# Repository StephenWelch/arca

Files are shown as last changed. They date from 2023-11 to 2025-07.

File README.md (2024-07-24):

## Members
Stephen Welch, Computer Engineering Student (2024)
stephenwelch@vt.edu

## Mentor
MENTOR NAME HERE

## Current Status
IN PROGRESS

### 7-24-24
- Prototype of full assembly design
- Work-in-progress hardware-sim abstraction layer
- Assembly & validation of updated left leg in progress
- Full model exported to URDF & MJCF
- Solved design issues:
  - Knee actuator didn't have enough clearance with sideplate to freely rotate
  - Knee joint was prone to friction with thigh sideplates
  - Thigh joint was prone to friction with lower thigh carriage
  - Hip motor mounting didn't have enough clearance to assemble without flex
  - Foot had no way to add rubber/other material for more friction
  - Width of knee joint made fastening bearings hard
- Current design issues:
  - Most fasteners are M3/M4 nuts & bolts - unknown how this will stand up to vibration
  - Rod end bearing range-of-motion is biggest limiter of robot range-of-motion
  - Backlash
    - Fasteners for 3D printed linkage arms to motor shaft have a lot of play
      - Linkage arm thru-hole tends to compress
        - Currently testing clamp-style design
      - M3 through motor shaft thru-hole is not perfect fit
        - May need to switch to steel pin
      - No off-the-shelf servo arms for motor shaft size
    - Several parts are very thin & flexible in the non-vertical direction in order to reduce size and make assembly easier
    - Mounting for thigh arms is not ideal & may flex
      - Planning on addressing this by integrating into thigh sideplates once finalized
  - Clearance and wire routing
    - Planning on investigating materials to reduce friction between motor wires & PLA parts

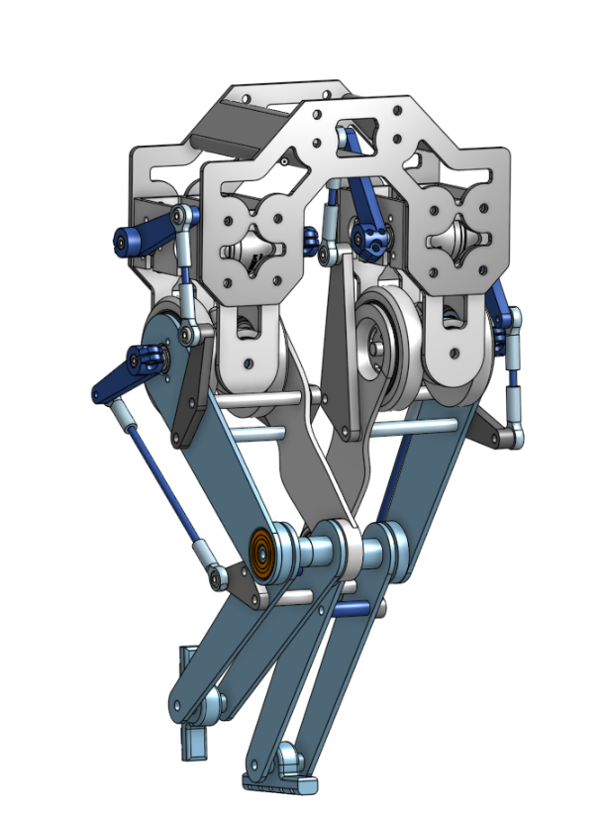
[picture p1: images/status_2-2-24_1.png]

  
### 2-2-24
- Test fit of (most of) 1st iteration design
- Waiting for electronics & test stand parts
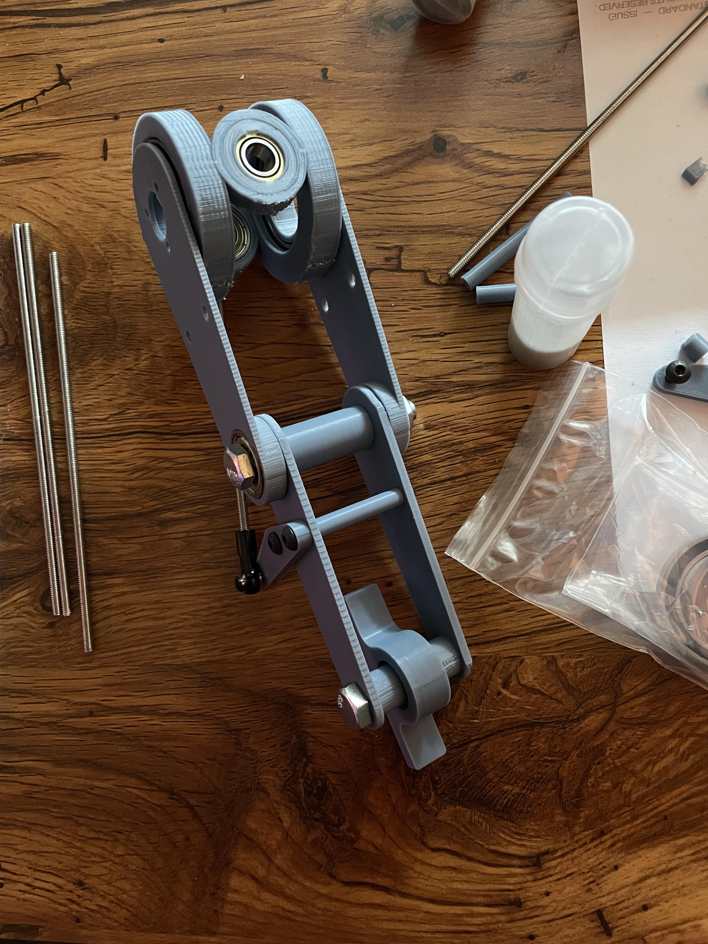
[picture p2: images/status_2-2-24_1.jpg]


## Project Overview

A torque-controlled bipedal robot for <$1000. The short term goal is assembling and validating a single leg under load.

## Educational Value Added

- Learning how to CAD complex moving assemblies
- Embedded controls
    - Implement torque control for robot joints
    - Serial interface to high-level controller
- High-level controls
    - ROS 2
    - Implementing [step timing adaptation-based walking controller](https://ieeexplore.ieee.org/stamp/stamp.jsp?arnumber=9082021)
    - Implementing [MPC walking control](https://arxiv.org/pdf/2010.08198.pdf)
    - Impedance control
    - Whole body control

## Tasks

<!-- Your Text Here. You may work with your mentor on this later when they are assigned -->

## Design Decisions

### Electronics
- Tethered operation to reduce cost
    - Battery, RPi, Power electronics to be added later
- Teensy commanded over serial by PC running high-level controller
- Robomaster M2006 P36 Brushless Motor
    - 1 Nm torque @ 1:36 reduction
    - 90g motor, 17g ESC
    - Pros:
      - Only brushless motor of its size supporting torque control out-of-the-box
      - [Proven performance](https://www.youtube.com/watch?v=_Sh4kRtmAog)
      - Constant torque at all RPMs
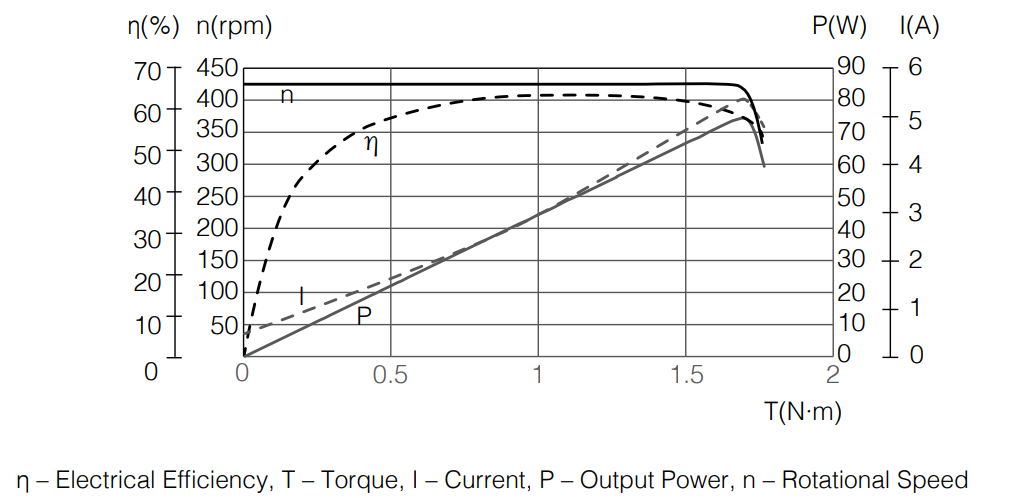
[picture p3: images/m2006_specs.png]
M2006 motor curves
        
    - Cons:
      - High reduction -> low torque transparency -> less compliance
      - Form factor challenging to package

### Mechanics
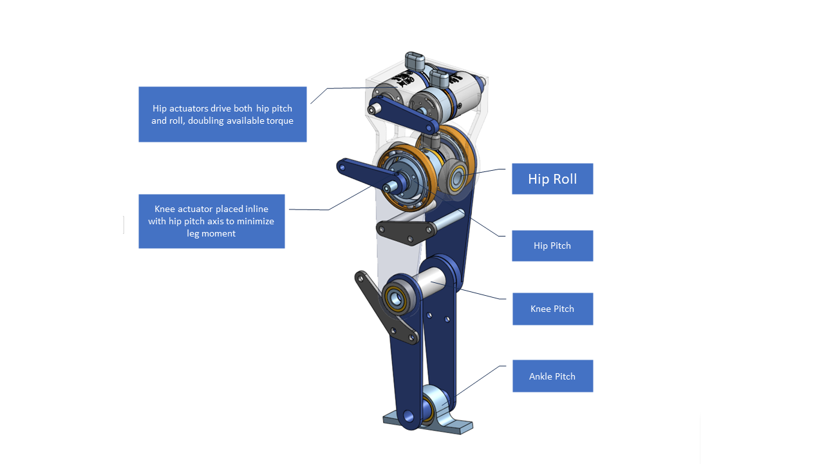
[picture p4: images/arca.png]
labeled diagram of leg

- 3 DoF per-leg
    - Pros:
        - Each actuator removed from the design saves $94
        - Reduces mechanical complexity
    - Cons:
        - Since the ankle isn't actuated, the robot is *not* passively stable - it must actively step to maintain balance
            - This makes control more challenging
        - Since hip yaw isn't actuated, the robot yaw can't be controlled directly while walking
- Actuator arrangement
    - Based on Tello Leg: [Video 1](https://www.youtube.com/watch?v=62lo04Up2vc) [Video 2](https://www.youtube.com/watch?v=mn8tCtYHzHI&t=1s) [Paper](https://arxiv.org/abs/2203.00644)
        - Challenging practical limitation to this design is rotor inertia of QDD actuators, especially at the knee/ankle differential. The P36 is not QDD and is much smaller scale, removing this limitation
    - Minimizes "reflected inertia" - the moment of inertia of each link the actuator has to move
    - Keeps knee actuator in the leg frame, which reduces torque tracking requirements
    - Combined hip/roll axes
        - Rarely actuated at the same time, effectively doubles available torque to 2 Nm
- Avoid gear/belt transmissions where possible
    - Large losses to friction, etc. esp. at this scale
    - Hard to get right, esp. with 3D prints
- Available torque
    - 1 N*m * 0.2248089431 lbf/N \* 100 cm/m = 22.48 lbf\*cm
    - Actuator linkages designed to be 1:1
    - Assuming 90 deg knee bend:
        - Knee can lift 22.48 lbf\*cm / 8 cm thigh length = 2.81 lbf
        - Thigh can lift 22.48 lbf\*cm * 2 motors / 8 cm thigh length = 5.62 lbf
        - Total weight of components is 107 g per actuator * 0.00220462 lbs/g * 3 actuators = 0.707685 lbs

## Design Misc

The main concern is that torque output won't be adequate for dynamic motions (the static case is addressed briefly above).
Possible fixes for this would include:
- Redesigning for larger, higher-torque actuators
- Designing a custom reduction for the M2006 motor
- Adding an effective reduction in the actuator linkages

## Steps for Documenting Your Design Process

<!-- Your Text Here. You may work with your mentor on this later when they are assigned -->

## BOM + Component Cost
[BOM Link](https://docs.google.com/spreadsheets/d/1Qe1dRF8I_yPayQ6RHrJmCSCA597qFWhmrA_jtBt1tgA/edit?usp=sharing)

## Timeline

[Timeline Link](timeline.pdf)

## Useful Links

[CAD](https://cad.onshape.com/documents/4743a97557c0a80d1585b0a7/w/2d6986bf76e2e55acb049bf2/e/10cf3b3fefc155c08becdc5d)
[C610 Motor Controller Library](https://github.com/stanfordroboticsclub/DJIC610Controller)
[BOLT Biped Driver](https://github.com/open-dynamic-robot-initiative/bolt)
[BRUCE Paper](https://ieeexplore.ieee.org/stamp/stamp.jsp?tp=&arnumber=9811790)

## Log

<!-- Your Text Here. You may work with your mentor on this later when they are assigned -->

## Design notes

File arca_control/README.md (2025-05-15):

# Arca Sim

Control code and simulator for the Arca biped.

## Getting started
- [Import a Model](#importing-a-model)
- [Start the simulator](#starting-the-simulation)

## Starting the simulation
Run `uv run scripts/sim.py --model <model_type>`, where `model_type` is a directory under `models`

## Importing a Model
Model paths follow this format: `models/<model_type>/<urdf|mjcf>`. 
- Each subfolder should have its own `config.json` for `onshape-to-robot`. 

Download the model into its corresponding path by running `uv run scripts/import_model.py --model <model_type>`. 

The available model types are:
- `full`: Models all linkages in the robot model
- `reduced`: Models only the pin joints of the robot

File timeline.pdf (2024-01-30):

PHASE ONE: Projected completion by Mar 2, 2024

The deliverable/objective of phase one is to complete a demonstration showing compliance between a motor controller and brushless dc motor. The objective is to write/implement the code required to allow for torque control on a teensy microcontroller. Must include bidirectional communication between microcontroller and motor controller such that the microcontroller uses the torque output to calculate a change in force applied by the motor.

Measure the torque applied by the motor on an actuator linkage. Demonstrate that a force of a specific magnitude can be generated.

This phase may be designed with the use of a harness as a power source instead of a battery.

This phase may include some 3D printing in order to build a linkage/joint. This phase require the design of the 3D printed linkages required to build the robot leg.

COST:

Part Name | Quantity | Unit Price
RM-C610 Brushless Motor Controller (https://store.dji.com/product/rm-c610-brushless-dc-motor-speed-control) | 1 $39.00
RM-M2006-C610 Brushless Motor (https://store.dji.com/product/rm-m2006-p36-brushless-motor) | 1 $55.00
Teensy 4.1 (https://www.amazon.com/PJRC-Teensy-4-1-Without-Pins/dp/B088D3FWR7)) | 1 | $34.60
6656K118 Ultra Thin Ball Bearing (https://www.mcmaster.com/products/bearings/ball-bearings~/ultra-thin-ball-bearings-6/) | 2 $15.65
Skate Bearings (https://www.amazon.com/gp/product/B08YN6WQXR/ref=sw_img_1?smid=AED51UXSJ2INU&psc=1) | 1 | $8.99
TOTAL | | $169.89 + tax/shipping

PHASE TWO: Projected Completion May 1, 2024

The deliverable is a complete robot leg. This leg will be composed of 3 motor/controller pairs each with torque control.

Demonstrate implementation of a walking algorithm successfully actuating the leg.

This phase will include the 3D printing of the parts required to build BOTH robot legs and the parts required to join the robot legs. This phase may include the design of the power electronics to operate the legs independently of a benchtop supply or may continue to use a benchtop supply.

COST: (ADDITIONAL PARTS TO PURCHASE)

Part Name | Quantity | Unit Price
RM-C610 Brushless Motor Controller (https://store.dji.com/product/rm-c610-brushless-dc-motor-speed-control) | 2 $39.00
RM-M2006-C610 Brushless Motor (https://store.dji.com/product/rm-m2006-p36-brushless-motor) | 2 $55.00
6656K118 Ultra Thin Ball Bearing (https://www.mcmaster.com/products/bearings/ball-bearings~/ultra-thin-ball-bearings-6/) | 2 $15.65
Skate Bearings (https://www.amazon.com/gp/product/B08YN6WQXR/ref=sw_img_1?smid=AED51UXSJ2INU&psc=1) | 1 | $8.99
TOTAL | | $228.29 + tax/shipping

PHASE THREE: Projected Completion TBD

Build a second leg. Use both legs together in order to demonstrate a functioning bipedal robot.

COST: TBD

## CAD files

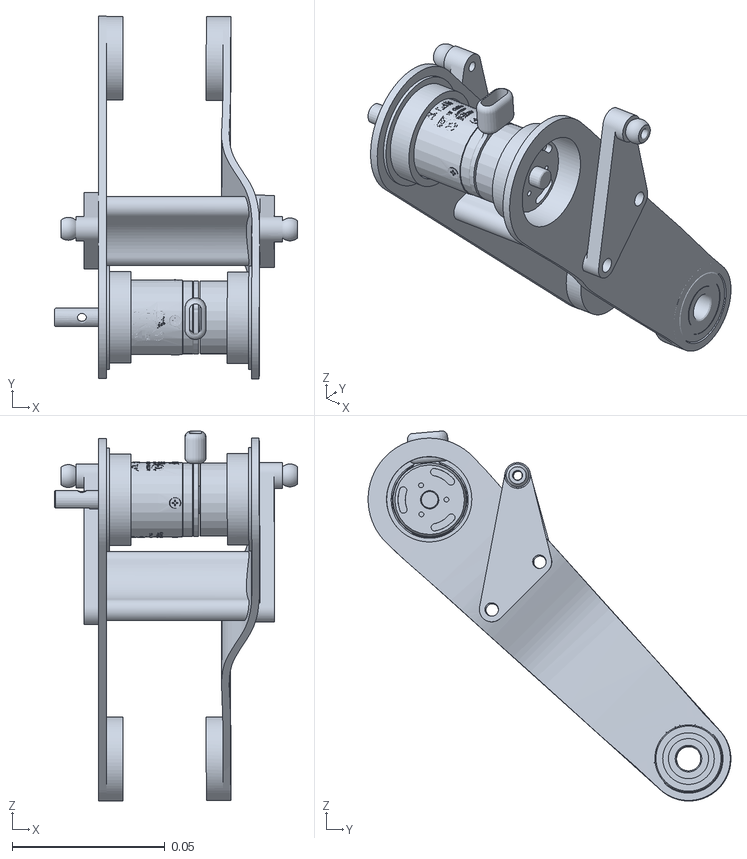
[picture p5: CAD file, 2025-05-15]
arca-sim/models/full/mjcf/assets/merged/r_thigh_visual.stl
0.0796 x 0.119 x 0.121

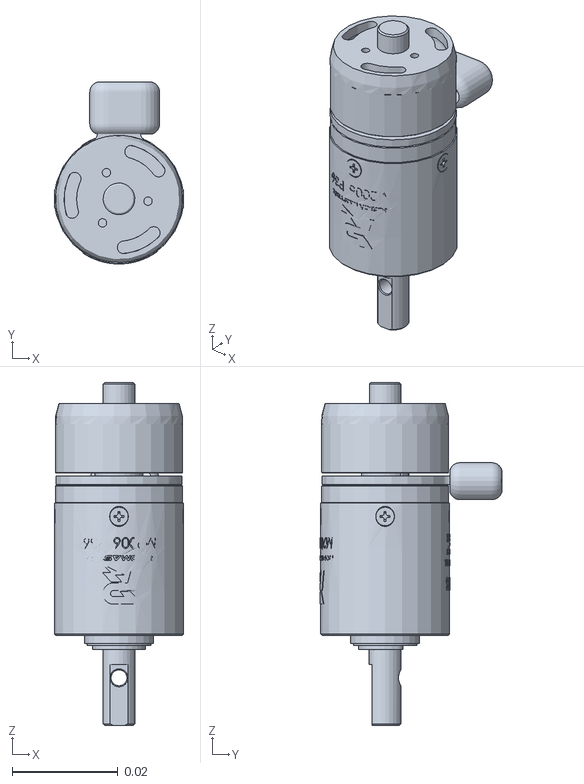
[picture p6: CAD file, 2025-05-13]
arca_control/models/full/mjcf/assets/m2006_p36_3.stl
0.0244 x 0.0344 x 0.0648

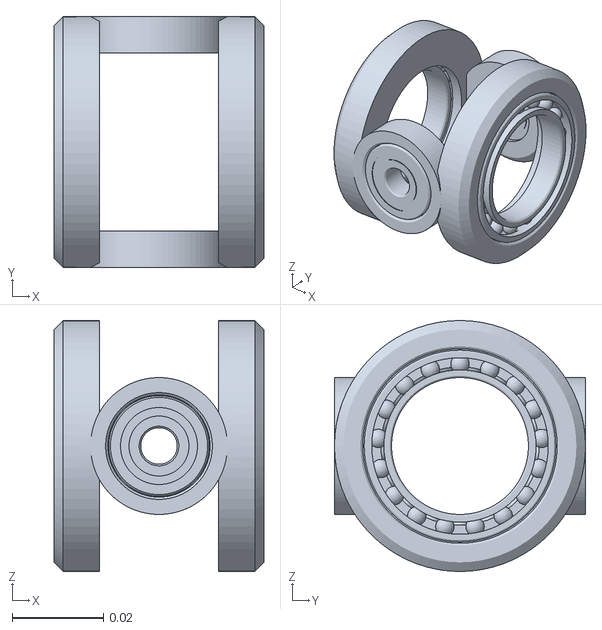
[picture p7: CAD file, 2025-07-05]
arca_control/models/full/mjcf/assets/merged/thigh_lower_mount_2_collision.stl
0.046 x 0.055 x 0.055

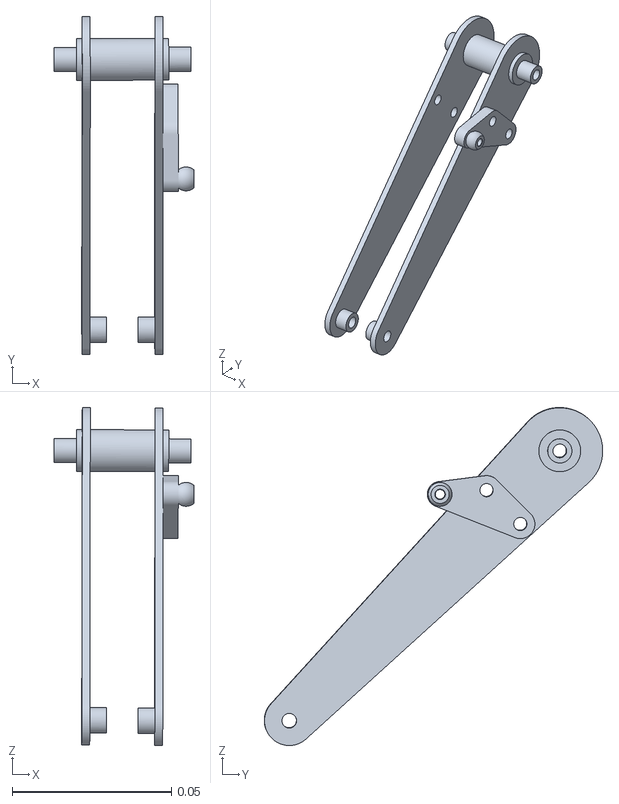
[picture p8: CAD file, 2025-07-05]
arca_rl/assets/assets/merged/l_knee_collision.stl
0.0439 x 0.106 x 0.106

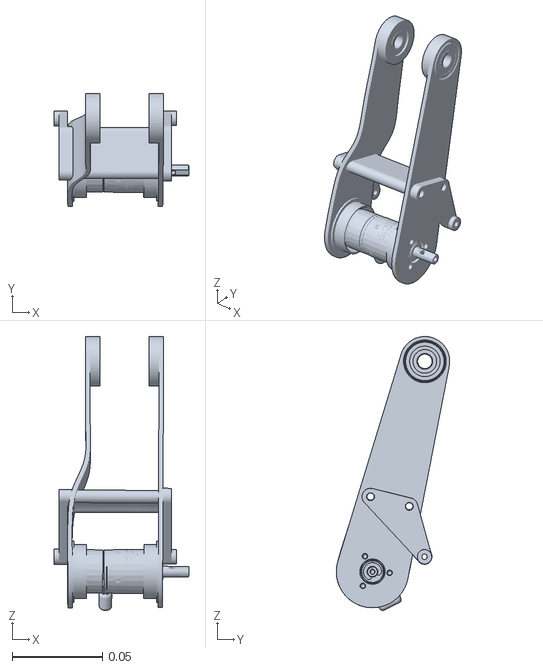
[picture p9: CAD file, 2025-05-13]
arca-sim/models/full/mjcf/assets/merged/r_thigh_collision.stl
0.0747 x 0.0628 x 0.152

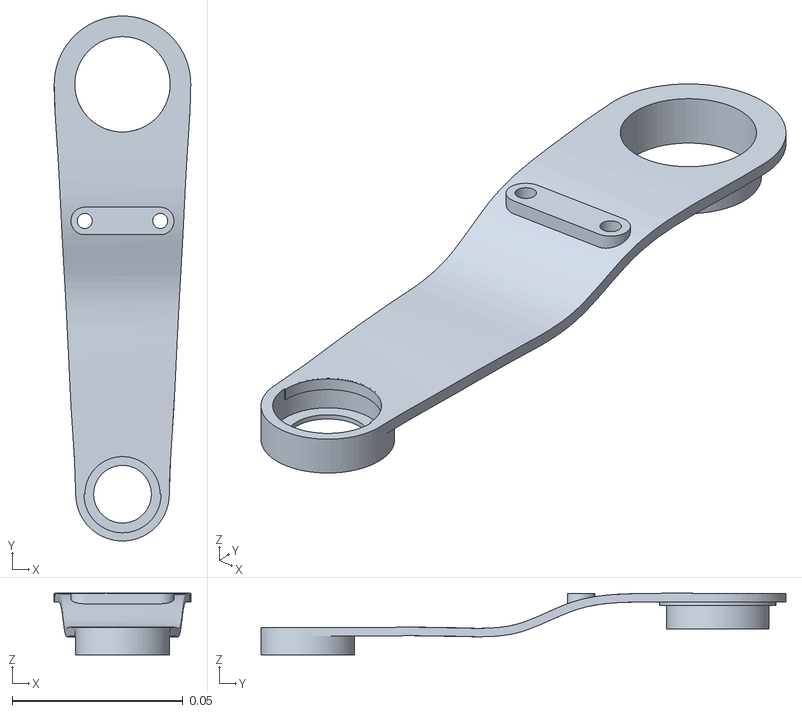
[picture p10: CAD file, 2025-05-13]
arca_control/models/full/mjcf/assets/l_inner_plate.stl
0.04 x 0.154 x 0.018

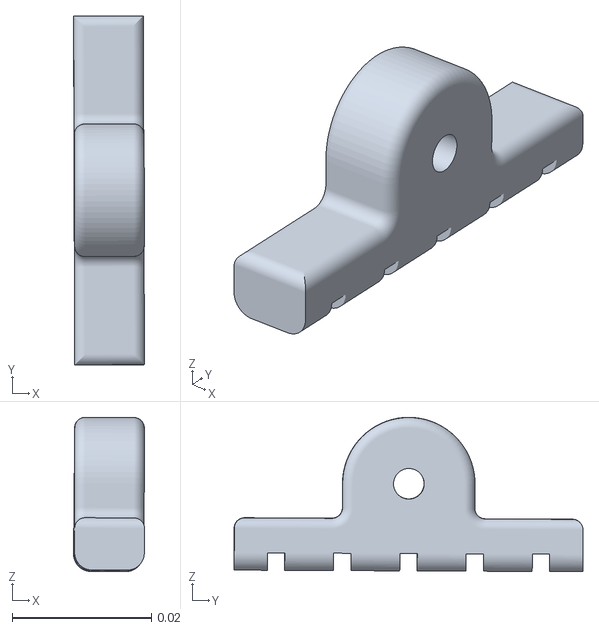
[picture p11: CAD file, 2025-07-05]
arca_rl/assets/assets/merged/foot_2_collision.stl
0.0102 x 0.0501 x 0.0221

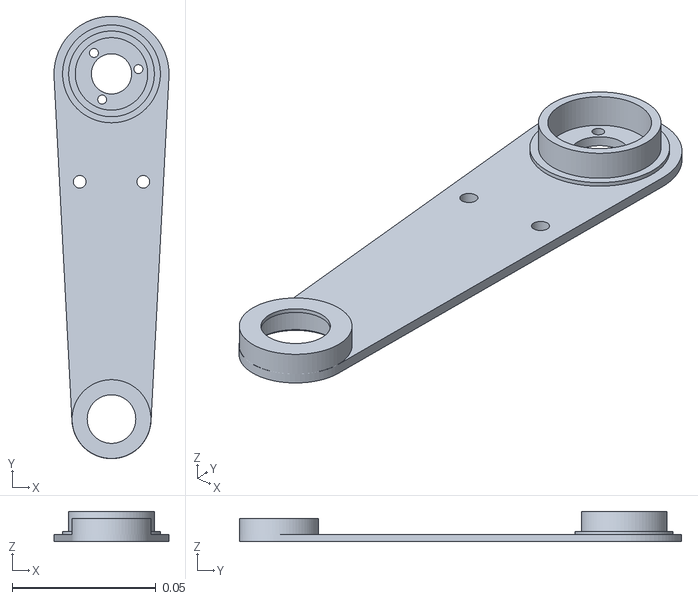
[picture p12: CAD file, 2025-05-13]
arca_rl/assets/assets/thigh__hip_arm_angle_2_356194490192345_radian.stl
0.04 x 0.154 x 0.0105

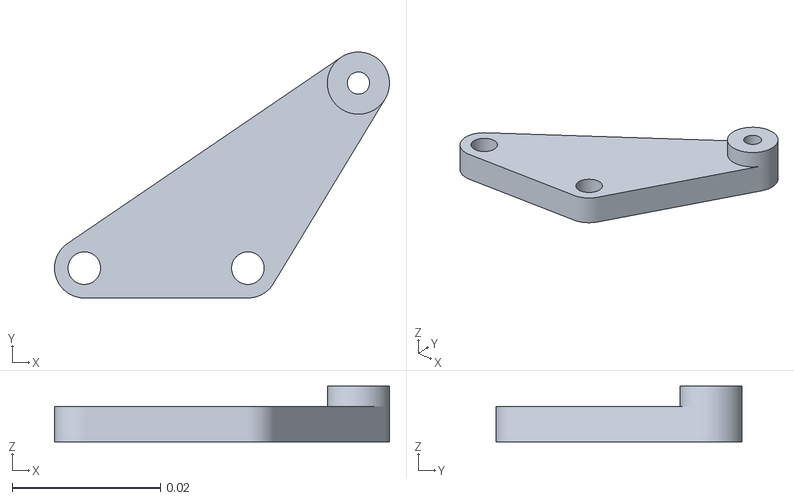
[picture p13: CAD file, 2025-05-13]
arca_control/models/full/mjcf/assets/r_inner_arm.stl
0.0453 x 0.0332 x 0.0075

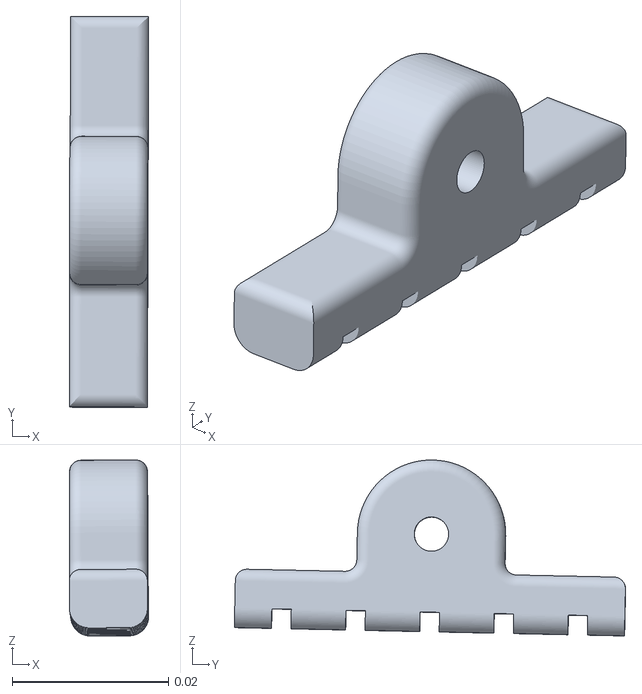
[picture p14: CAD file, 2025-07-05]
arca_rl/assets/assets/merged/foot_visual.stl
0.0102 x 0.0501 x 0.0226

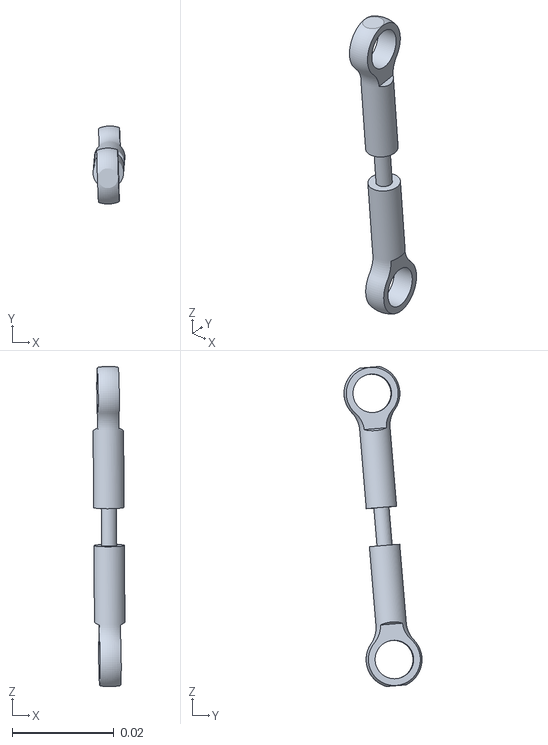
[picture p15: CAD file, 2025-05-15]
arca_control/models/full/mjcf/assets/merged/linkage__43d788dc267bdd7f4fb3b94dc32a7642_2_visual.stl
0.00627 x 0.0153 x 0.0629

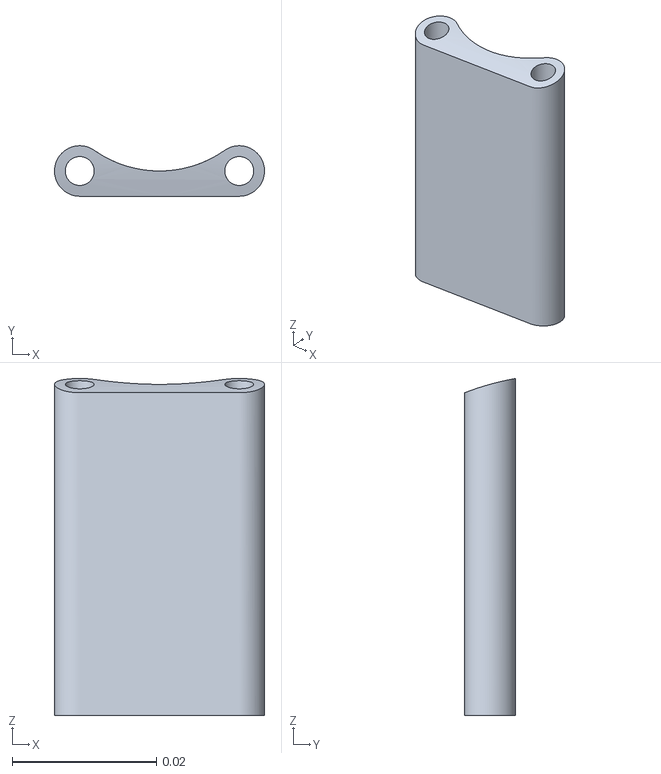
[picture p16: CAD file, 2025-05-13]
arca_control/models/full/mjcf/assets/standoff.stl
0.0291 x 0.007 x 0.0467

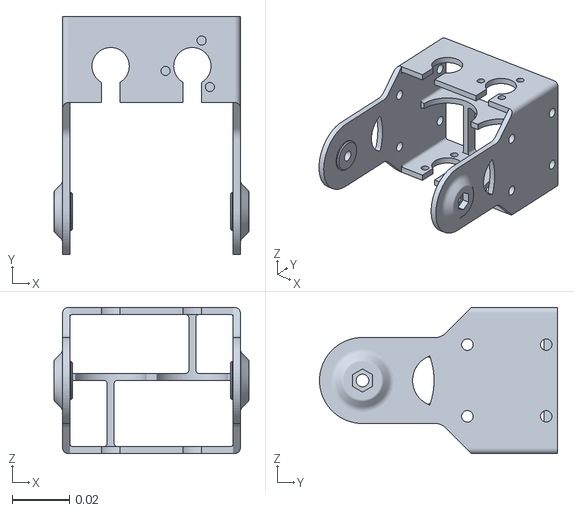
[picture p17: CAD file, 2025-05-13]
arca_rl/assets/assets/upper_carriage__2.stl
0.068 x 0.083 x 0.051

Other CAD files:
arca_rl/assets/assets/m2006_p36_3.stl
arca_control/models/full/mjcf/assets/merged/thigh_lower_mount_visual.stl
arca_control/models/full/mjcf/assets/merged/thigh_lower_mount_collision.stl
arca_rl/assets/assets/m2006_p36_3__3.stl
arca-sim/models/full/mjcf/assets/6656k118_ultra_thin_ball_bearing.stl
arca_control/models/full/mjcf/assets/59935k13_ball_joint_rod_end__2.stl
arca_control/models/full/mjcf/assets/hip_arm__length_0_04_meter.stl
arca_control/models/full/mjcf/assets/l_inner_arm.stl
arca_control/models/full/mjcf/assets/l_outer_arm.stl
arca_control/models/full/mjcf/assets/l_outer_plate.stl
arca_control/models/full/mjcf/assets/merged/foot_2_collision.stl
arca_control/models/full/mjcf/assets/merged/foot_2_visual.stl
arca_control/models/full/mjcf/assets/merged/foot_collision.stl
arca_control/models/full/mjcf/assets/merged/foot_visual.stl
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

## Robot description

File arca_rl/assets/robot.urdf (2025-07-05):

<?xml version="1.0" ?>
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
<robot name="urdf">
  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
  <link name="trunk">
    <inertial>
      <origin xyz="8.93209e-17 -0.0322521 -0.0255515" rpy="0 0 0"/>
      <mass value="0.50738"/>
      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
    </inertial>
    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
  </link>
  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
  <link name="thigh_lower_mount">
    <inertial>
      <origin xyz="-1.12935e-18 -1.75427e-05 -0.0275" rpy="0 0 0"/>
      <mass value="0.106222"/>
      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
    </inertial>
    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
  </link>
  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
  <link name="r_thigh">
    <inertial>
      <origin xyz="0.000352109 -0.0299392 0.017919" rpy="0 0 0"/>
      <mass value="0.156403"/>
      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
    </inertial>
    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
  </link>
  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
  <link name="r_knee">
    <inertial>
      <origin xyz="-0.00131403 -0.0427728 -0.0165918" rpy="0 0 0"/>
      <mass value="0.0251199"/>
      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
    </inertial>
    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
  </link>
  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
  <link name="foot">
    <inertial>
      <origin xyz="-8.30386e-08 -0.00450828 -0.005" rpy="0 0 0"/>
      <mass value="0.00685832"/>
      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
    </inertial>
    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
  </link>
  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
  <joint name="r_ankle_passive" type="revolute">
    <origin xyz="-3.05311e-16 -0.12 -0.0195" rpy="3.14159 3.34686e-16 -2.34644"/>
    <parent link="r_knee"/>
    <child link="foot"/>
    <axis xyz="0 0 1"/>
    <limit effort="10" velocity="10" lower="-3.141592653589793" upper="3.141592653589793"/>
  </joint>
  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
  <joint name="r_knee" type="revolute">
    <origin xyz="-1.40571e-06 -0.119866 0.032731" rpy="-0.000473435 -0.00530076 -1.48248"/>
    <parent link="r_thigh"/>
    <child link="r_knee"/>
    <axis xyz="0 0 1"/>
    <limit effort="10" velocity="10" lower="-3.141592653589793" upper="3.141592653589793"/>
  </joint>
  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
  <joint name="r_hip_pitch" type="revolute">
    <origin xyz="-0.023 4.16334e-17 -0.0275" rpy="-1.5708 -0.904819 -1.5708"/>
    <parent link="thigh_lower_mount"/>
    <child link="r_thigh"/>
    <axis xyz="0 0 1"/>
    <limit effort="10" velocity="10" lower="-3.141592653589793" upper="3.141592653589793"/>
  </joint>
  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
  <joint name="r_hip_roll" type="revolute">
    <origin xyz="-0.05175 -0.00475 -0.0806645" rpy="-1.5708 -1.66533e-16 -2.19958e-17"/>
    <parent link="trunk"/>
    <child link="thigh_lower_mount"/>
    <axis xyz="0 0 1"/>
    <limit effort="10" velocity="10" lower="-3.141592653589793" upper="3.141592653589793"/>
  </joint>
  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
  <link name="thigh_lower_mount_2">
    <inertial>
      <origin xyz="-3.88721e-18 -1.75427e-05 -0.0275" rpy="0 0 0"/>
      <mass value="0.106222"/>
      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
    </inertial>
    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
  </link>
  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
  <link name="l_thigh">
    <inertial>
      <origin xyz="-0.000312941 -0.0299249 0.017919" rpy="0 0 0"/>
      <mass value="0.156403"/>
      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
    </inertial>
    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
  </link>
  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
  <link name="l_knee">
    <inertial>
      <origin xyz="0.00122988 -0.0428518 -0.016707" rpy="0 0 0"/>
      <mass value="0.0251199"/>
      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
    </inertial>
    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
  </link>
  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
  <link name="foot_2">
    <inertial>
      <origin xyz="-8.30386e-08 -0.00450828 -0.005" rpy="0 0 0"/>
      <mass value="0.00685832"/>
      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
    </inertial>
    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
  </link>
  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
  <joint name="l_ankle_passive" type="revolute">
    <origin xyz="4.44089e-16 -0.12 -0.0195" rpy="-3.14159 -1.73512e-15 2.35962"/>
    <parent link="l_knee"/>
    <child link="foot_2"/>
    <axis xyz="0 0 1"/>
    <limit effort="10" velocity="10" lower="-3.141592653589793" upper="3.141592653589793"/>
  </joint>
  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
  <joint name="l_knee" type="revolute">
    <origin xyz="-1.40571e-06 -0.119866 0.032731" rpy="-0.000717208 0.00527331 1.43485"/>
    <parent link="l_thigh"/>
    <child link="l_knee"/>
    <axis xyz="0 0 1"/>
    <limit effort="10" velocity="10" lower="-3.141592653589793" upper="3.141592653589793"/>
  </joint>
  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
  <joint name="l_hip_pitch" type="revolute">
    <origin xyz="-0.023 2.77556e-17 -0.0275" rpy="-1.5708 0.922339 -1.5708"/>
    <parent link="thigh_lower_mount_2"/>
    <child link="l_thigh"/>
    <axis xyz="0 0 1"/>
    <limit effort="10" velocity="10" lower="-3.141592653589793" upper="3.141592653589793"/>
  </joint>
  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
  <joint name="l_hip_roll" type="revolute">
    <origin xyz="0.05175 -0.00475 -0.0806645" rpy="1.5708 -1.9322e-05 -3.14159"/>
    <parent link="trunk"/>
    <child link="thigh_lower_mount_2"/>
    <axis xyz="0 0 1"/>
    <limit effort="10" velocity="10" lower="-3.141592653589793" upper="3.141592653589793"/>
  </joint>
</robot>

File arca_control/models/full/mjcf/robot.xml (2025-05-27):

<?xml version="1.0" ?>
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
<mujoco model="C:\Users\steph\code\arca\arca-sim\models\full\mjcf">
  <compiler angle="radian" meshdir="assets" autolimits="true"/>
  <default>
    <default class="C:\Users\steph\code\arca\arca-sim\models\full\mjcf">
      <joint frictionloss="0.1" armature="0.005"/>
      <position kp="50" dampratio="1"/>
      <default class="visual">
        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
      </default>
      <default class="collision">
        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
      </default>
    </default>
  </default>
  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
  <default>
    <equality solimp="0.9 0.95 0.001 0.5 2" solref="0.005 1"/>
  </default>
  <worldbody>
    <body name="world_link" pos="0 0 0" quat="1 0 0 0"/>
  </worldbody>
  <equality>
    <weld name="gantry" body1="world_link" body2="trunk" relpose="0 0 0.272 1 0 0 0"/>
  </equality>
  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
  <option timestep="0.001"/>
  <worldbody>
    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
    <body name="trunk" pos="0 0 0" quat="1 0 0 0" childclass="C:\Users\steph\code\arca\arca-sim\models\full\mjcf">
      <freejoint name="trunk_freejoint"/>
      <inertial pos="-2.1021e-06 5.76953e-17 -0.0342193" mass="0.50738" fullinertia="0.00154489 0.000361696 0.00155102 6.30203e-08 8.81145e-09 4.36525e-07"/>
      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
      <body name="thigh_lower_mount" pos="0.0275 -0.05175 -0.0893322" quat="0.5 0.5 0.5 0.5">
        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
        <joint axis="0 0 1" name="l_hip_roll_passive" type="hinge" frictionloss="0.01"/>
        <inertial pos="3.97415e-18 -1.75427e-05 -0.0275" mass="0.106222" fullinertia="4.98391e-05 6.15836e-05 4.69705e-05 -6.46051e-20 -2.14174e-13 4.25848e-13"/>
        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
        <body name="l_thigh" pos="-0.02275 -8.04912e-16 -0.0275" quat="0.270598 0.653281 0.270598 0.653281">
          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
          <joint axis="0 0 1" name="l_hip_pitch_passive" type="hinge" frictionloss="0.01"/>
          <inertial pos="0.000899952 0.0298613 0.0179928" mass="0.15874" fullinertia="0.000394916 6.10091e-05 0.00035582 2.95051e-06 2.80027e-07 4.27413e-07"/>
          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
          <body name="l_knee" pos="2.49973e-06 0.119861 0.032728" quat="0.707094 0.00186181 0.00185503 -0.707114">
            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
            <joint axis="0 0 1" name="l_knee_passive" type="hinge" frictionloss="0.01"/>
            <inertial pos="0.00122988 -0.0428518 -0.016707" mass="0.0251199" fullinertia="4.11528e-05 4.86011e-06 3.88399e-05 -2.3273e-07 4.94116e-07 5.96743e-07"/>
            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
            <body name="foot" pos="1.69309e-15 -0.12 -0.0195" quat="5.71162e-16 -1 -3.52872e-15 -8.33754e-16">
              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
              <joint axis="0 0 1" name="l_ankle_passive" type="hinge" frictionloss="0.01"/>
              <inertial pos="-0.00318778 0.00318789 -0.005" mass="0.00685832" fullinertia="6.32237e-07 6.32238e-07 1.15532e-06 -3.568e-07 3.9418e-13 3.69545e-13"/>
              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
            </body>
          </body>
          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
          <body name="knee_arm__length_0_04_meter" pos="0 2.77556e-17 -0.018" quat="0.34202 -6.08221e-15 2.55351e-15 -0.939693">
            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
            <joint axis="0 0 1" name="l_knee" type="hinge" frictionloss="0.01"/>
            <inertial pos="0.0192583 -0.00522325 0.0091877" mass="0.00480721" fullinertia="1.96137e-07 1.3472e-06 1.41312e-06 3.3253e-07 -2.06002e-07 5.48122e-08"/>
            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
            <body name="l_knee_passive_link_x" pos="0.0386177 -0.0104248 0.013825" quat="0.129379 -0.89705 -0.416511 0.0712861">
              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
              <joint axis="1 0 0" name="l_knee_passive_x" type="hinge" frictionloss="0.01"/>
              <inertial pos="0 0 0" mass="1e-09" fullinertia="1e-09 1e-09 1e-09 0 0 0"/>
              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
              <body name="l_knee_passive_link_y" pos="0 0 -6.93889e-18" quat="1 -0 -2.77556e-17 -2.42861e-17">
                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
                <joint axis="0 1 0" name="l_knee_passive_y" type="hinge" frictionloss="0.01"/>
                <inertial pos="0 0 0" mass="1e-09" fullinertia="1e-09 1e-09 1e-09 0 0 0"/>
                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
                <body name="linkage__configuration_default_length_0_12_meter" pos="0 0 -6.93889e-18" quat="1 -0 -2.77556e-17 -2.42861e-17">
                  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
                  <joint axis="0 0 1" name="l_knee_passive_z" type="hinge" frictionloss="0.01"/>
                  <inertial pos="-0.06 -5.19278e-09 1.72691e-15" mass="0.00554627" fullinertia="1.40646e-08 5.38143e-06 5.37746e-06 -3.28364e-20 -9.69161e-12 -1.62539e-19"/>
                  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
                </body>
              </body>
            </body>
          </body>
        </body>
      </body>
      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
      <body name="thigh_lower_mount_2" pos="0.0275 0.05175 -0.0893322" quat="0.5 -0.5 0.5 -0.5">
        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
        <joint axis="0 0 1" name="r_hip_roll_passive" type="hinge" frictionloss="0.01"/>
        <inertial pos="-1.06588e-18 -1.75427e-05 -0.0275" mass="0.106222" fullinertia="4.98391e-05 6.15836e-05 4.69705e-05 1.32733e-20 -2.14174e-13 4.25849e-13"/>
        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
        <body name="r_thigh" pos="-0.02275 -4.16334e-17 -0.0275" quat="0.653281 0.270598 0.653281 0.270598">
          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
          <joint axis="0 0 1" name="r_hip_pitch_passive" type="hinge" frictionloss="0.01"/>
          <inertial pos="-0.000931108 0.0298878 0.0179928" mass="0.15874" fullinertia="0.000394556 6.11092e-05 0.000355559 -3.13013e-06 -2.2953e-07 3.84008e-07"/>
          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
          <body name="r_knee" pos="2.49973e-06 0.119861 0.032728" quat="0.707114 0.00185503 -0.00186181 0.707094">
            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
            <joint axis="0 0 1" name="r_knee_passive" type="hinge" frictionloss="0.01"/>
            <inertial pos="-0.00122513 -0.0428542 -0.0167069" mass="0.0251199" fullinertia="4.1152e-05 4.85627e-06 3.88354e-05 2.31027e-07 -4.92054e-07 5.95733e-07"/>
            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
            <body name="foot_2" pos="3.38618e-15 -0.12 -0.0195" quat="7.0633e-16 -0.382683 0.92388 -3.35573e-16">
              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
              <joint axis="0 0 1" name="r_ankle_passive" type="hinge" frictionloss="0.01"/>
              <inertial pos="-8.30386e-08 -0.00450828 -0.005" mass="0.00685832" fullinertia="2.75437e-07 9.89038e-07 1.15532e-06 8.01075e-13 -5.40036e-13 1.74194e-14"/>
              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
            </body>
          </body>
          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
          <body name="knee_arm__length_0_04_meter_2" pos="-2.8365e-05 -3.38041e-05 -0.018" quat="0.34202 1.17314e-15 -7.77156e-15 0.939693">
            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
            <joint axis="0 0 1" name="r_knee" type="hinge" frictionloss="0.01"/>
            <inertial pos="-0.0192516 -0.005248 0.0091877" mass="0.00480721" fullinertia="2.0089e-07 1.34244e-06 1.41312e-06 -3.40624e-07 2.05393e-07 5.70504e-08"/>
            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
            <body name="r_knee_passive_link_x" pos="-0.0385793 -0.0105658 0.013825" quat="0.245803 0.34382 0.75087 0.507506">
              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
              <joint axis="1 0 0" name="r_knee_passive_x" type="hinge" frictionloss="0.01"/>
              <inertial pos="0 0 0" mass="1e-09" fullinertia="1e-09 1e-09 1e-09 0 0 0"/>
              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
              <body name="r_knee_passive_link_y" pos="6.93889e-18 0 0" quat="1 -9.02897e-18 5.55112e-17 -2.77556e-17">
                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
                <joint axis="0 1 0" name="r_knee_passive_y" type="hinge" frictionloss="0.01"/>
                <inertial pos="0 0 0" mass="1e-09" fullinertia="1e-09 1e-09 1e-09 0 0 0"/>
                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
                <body name="linkage__configuration_default_length_0_12_meter_2" pos="6.93889e-18 0 0" quat="1 -9.02897e-18 5.55112e-17 -2.77556e-17">
                  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
                  <joint axis="0 0 1" name="r_knee_passive_z" type="hinge" frictionloss="0.01"/>
                  <inertial pos="-0.06 -5.19278e-09 -1.15678e-17" mass="0.00554627" fullinertia="1.40646e-08 5.38143e-06 5.37746e-06 -3.34755e-20 -9.69161e-12 -1.09556e-20"/>
                  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
                </body>
              </body>
            </body>
          </body>
        </body>
      </body>
      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

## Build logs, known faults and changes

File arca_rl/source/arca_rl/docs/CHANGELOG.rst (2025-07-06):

Changelog
---------

0.1.0 (2025-07-04)
~~~~~~~~~~~~~~~~~~

Added
^^^^^

* Created an initial template for building an extension or project based on Isaac Lab

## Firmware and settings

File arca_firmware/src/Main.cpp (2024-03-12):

//
// Created by Stephen Welch on 2/27/2024.
//
#include "Arduino.h"
#include "C610.h"
#include "C610Bus.h"
#include "SoftwareTimer.h"
#include "BasicLinearAlgebra.h"
#include "Kinematics.h"

enum ControlMode
{
    kJointPosition = 'p',
    kEndEffectorPosition = 'e',
    kEndEffectorForce = 'f',
    kTorque = 't',
    kCurrent = 'c',
};

const float CW_JOINT_LIMIT = radians(0);
const float CCW_JOINT_LIMIT = radians(115);

const BLA::Matrix<3, 3> endEffectorPositionGains = {
    100.0, 0.0, 0.0,
    0.0, 100.0, 0.0,
    0.0, 0.0, 100.0
};

const BLA::Matrix<3, 3> endEffectorVelocityGains = {
    5.0, 0.0, 0.0,
    0.0, 5.0, 0.0,
    0.0, 0.0, 5.0
};

// program resources
C610Bus<CAN1> bus; // Initialization. Templated to either use CAN1 or CAN2.
Timer printTimer(50);
Timer controlTimer(1000);

// program state
int id = 0;
bool firstLoop = true;
bool motorsEnabled = true;
ControlMode mode = kCurrent;
BLA::Matrix<3> torque = {0, 0, 0};
BLA::Matrix<3> force = {0, 0, 0};
int32_t currentCommands[] = {0, 0, 0, 0, 0, 0, 0, 0};

// control state
BLA::Matrix<3> endEffectorPos = {0, 0, 0};
BLA::Matrix<3> endEffectorVel = {0, 0, 0};
float desiredJointPos = 0;
float desiredTorque = 0;
float desiredCurrent = 0;
BLA::Matrix<3> desiredEndEffectorPos = {0, 0, 0};
BLA::Matrix<3> desiredEndEffectorForce = {0, 0, 0};

void setup()
{
    Serial.begin(115200);
    Serial.println("g <motor_id> to start telemetry, s to stop");

    controlTimer.start();
}


inline void printVariable(const String& name, const float val)
{
    String s;
    s = name + ":" + String(val) + " ";
    Serial.print(s);
}

template <typename DerivedType, int rows, int cols, typename d_type>
void printMatrix(const String& name, const BLA::MatrixBase<DerivedType, rows, cols, d_type>& m)
{
    for (int r = 0; r < rows; r++)
    {
        for (int c = 0; c < cols; c++)
        {
            Serial.print(name);
            Serial.print("_");
            Serial.print(r);
            Serial.print(c);
            Serial.print(": ");
            Serial.print(m(r, c));
            Serial.print(" ");
        }
    }
}

inline int sign(float val) { return (val > 0) - (val < 0); }

/**
 * \brief
 * \param torque Torque in Nm
 * \return Current in mA
 */
int32_t torqueToCurrent(double torque, C610& motor)
{
    double ff, kV, kI;
    if (motor.Velocity() * motor.Current() > 0)
    {
        // forward/backward
        ff = -0.0673;
        kV = -0.00277;
        kI = 0.000308;
    }
    else
    {
        // backdriving
        ff = -0.0136;
        kV = -0.00494;
        kI = 0.000179;
    }

    return static_cast<int32_t>((torque - ff * sign(motor.Velocity()) - kV * motor.Velocity()) / kI);
    // return static_cast<int32_t>((torque - ff * motor.Velocity()) / kI);
}

void loop()
{
    if (Serial.available() > 0)
    {
        String cmd = Serial.readString().trim();
        switch (cmd[0])
        {
        case 'g':
            if (cmd.length() >= 3)
            {
                int requested_id = cmd.substring(2).toInt();
                if (requested_id >= 0 && requested_id <= 7)
                {
                    id = requested_id;
                }
                else
                {
                    Serial.print("Motor ID ");
                    Serial.print(requested_id);
                    Serial.println("outside of range 1-8");
                }
            }

            Serial.println("Started");
            printTimer.start();
            break;
        case 's':
            Serial.println("Stopped");
            printTimer.stop();
            break;
        case 'a':
            motorsEnabled = !motorsEnabled;
            Serial.print(motorsEnabled ? "Motors enabled" : "Motors disabled");
            break;
        case kCurrent:
            mode = kCurrent;
            if (cmd.length() >= 3) desiredCurrent = cmd.substring(2).toFloat();
            break;
        case kTorque:
            mode = kTorque;
            if (cmd.length() >= 3) desiredTorque = cmd.substring(2).toFloat();
            break;
        case kJointPosition:
            mode = kJointPosition;
            if (cmd.length() >= 3) desiredJointPos = cmd.substring(2).toFloat();
            break;
        case kEndEffectorPosition:
            mode = kEndEffectorPosition;
            if (cmd.length() >= 3) desiredEndEffectorPos(2) = cmd.substring(2).toFloat();
            break;
        case kEndEffectorForce:
            mode = kEndEffectorForce;
            if (cmd.length() >= 3) desiredEndEffectorForce(2) = cmd.substring(2).toFloat();
            break;
        default:
            Serial.print("Command char '");
            Serial.print(cmd[0]);
            Serial.println("' is not valid");
            break;
        }
    }

    bus.PollCAN(); // Check for messages from the motors.

    if (controlTimer.update())
    {
        C610& motor = bus.Get(id);
        endEffectorPos = ForwardKinematics({0, 0, motor.Position()}, {}, 0);
        auto jac = LegJacobian({0, 0, motor.Position()}, {}, 0);
        endEffectorVel = jac * BLA::Matrix<3>{0, motor.Velocity(), 0};

        if (firstLoop)
        {
            firstLoop = false;
            desiredEndEffectorPos = endEffectorPos;
        }

        switch (mode)
        {
        case kCurrent:
            currentCommands[id] = static_cast<int32_t>(desiredCurrent * 1000);
            break;
        case kTorque:
            currentCommands[id] = torqueToCurrent(desiredTorque, motor);
            break;
        case kJointPosition:
            torque(2) = 1.5 * (desiredJointPos - motor.Position()) - 0.1 * motor.Velocity(); // PD position control
            currentCommands[id] = torqueToCurrent(torque(2), motor);
            break;
        case kEndEffectorPosition:
            desiredEndEffectorPos(0) = endEffectorPos(0);
            force = endEffectorPositionGains * (desiredEndEffectorPos - endEffectorPos) - endEffectorVelocityGains * endEffectorVel;
            torque = (~jac * force);
            currentCommands[id] = torqueToCurrent(torque(2), motor);
        // currentCommands[id] = static_cast<int32_t>(torque(2)*1000);
        // Serial.println(currentCommands[id]);
        // currentCommands[id] = 0;
        // printMatrix("force", force);
        // printMatrix("torque", torque);
        // printMatrix("jac", ~jac);
        // Serial.println();

            break;
        case kEndEffectorForce:
            torque = (~jac * desiredEndEffectorForce);
            currentCommands[id] = torqueToCurrent(torque(2), motor);
            // currentCommands[id] = static_cast<int32_t>(torque(2) * 1000);
            break;
        }

        // prevent motors from moving in direction past joint limits
        if (motor.Position() < CW_JOINT_LIMIT && currentCommands[id] < 0)
        {
            currentCommands[id] = 0;
        }
        if( motor.Position() > CCW_JOINT_LIMIT && currentCommands[id] > 0)
        {
            currentCommands[id] = 0;
        }
        if( !motorsEnabled )
        {
            currentCommands[id] = 0;
        }

        // current limit
        currentCommands[id] = constrain(currentCommands[id], -2000, 2000);

        bus.CommandTorques(currentCommands[0], currentCommands[1], currentCommands[2], currentCommands[3],
                           C610Subbus::kOneToFourBlinks);
        bus.CommandTorques(currentCommands[4], currentCommands[5], currentCommands[6], currentCommands[7],
                           C610Subbus::kFiveToEightBlinks);
    }

    if (printTimer.update())
    {
        C610& motor = bus.Get(id);

        printVariable("mode", mode);
        printVariable("pos", degrees(motor.Position()));
        // printVariable(id, "vel", motor.Velocity());
        // printVariable(id, "current", motor.Current());
        printVariable("torque", motor.Torque());
        printMatrix("force", force);
        controlTimer.print();
        // printTimer.print();
        printVariable("des_joint_pos", desiredJointPos);
        printVariable("cmd", currentCommands[id]);
        printMatrix("cmd_t", torque);
        // printVariable(id, "des_joint_x", desiredEndEffectorPos(0));
        // printVariable(id, "des_joint_y", desiredEndEffectorPos(1));
        printVariable("des_joint_z", desiredEndEffectorPos(2));
        printVariable("x", endEffectorPos(0));
        printVariable("y", endEffectorPos(1));
        printVariable("z", endEffectorPos(2));
        Serial.println();
    }
}

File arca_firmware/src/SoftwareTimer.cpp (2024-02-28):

//
// Created by Stephen Welch on 2/22/2024.
//

#include "SoftwareTimer.h"
#include "Arduino.h"

Timer::Timer(float rate) {
    this->period = static_cast<uint32_t>(1000000 / rate);
    this->running = false;
    this->startTime = 0;
    this->currentTime = 0;
    this->timeElapsed = 0;
}

void Timer::start() {
    this->running = true;
    this->reset();
}

void Timer::stop()
{
    this->running = false;
}

void Timer::reset() {
    this->startTime = micros();
}

bool Timer::update()
{
    if(!this->running) return false;

    currentTime = micros();
    const uint32_t timeElapsed = currentTime - this->startTime;
    if(timeElapsed >= this->period)
    {
        this->timeElapsed = timeElapsed;
        this->reset();
        return true;
    }
    return false;
}

uint32_t Timer::getTimeElapsed() const
{
    return this->timeElapsed;
}

uint32_t Timer::getPeriod() const
{
    return this->period;
}

double Timer::getActualRate() const
{
    return 1000000.0 / this->getTimeElapsed();
}


void Timer::print() const
{
    Serial.print("timer_");
    Serial.print(this->getPeriod());
    Serial.print(":");
    Serial.print(this->getActualRate());
    Serial.print(" ");
}

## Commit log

2023-10-20 Add CAD link
2024-02-28 Print measured Timer rate
2024-02-28 Add control modes & test forward kinematics
2024-02-28 Add current control mode
2024-02-28 Add ArduinoJson dependency
2024-03-12 Add motor enable/disable so we can watch controller outputs
2024-07-30 Add scene
    [scene.xml]
2025-05-13 Switch to uv
2025-05-13 Update full and reduced onshape export
    [5972k222_ball_bearing.stl, 5972k222_ball_bearing__2.stl, 59935k13_ball_joint_rod_end.stl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]
2025-05-13 Add gantry release to viewer
2025-05-13 Switch to effort actuators
    [extras.xml, robot.xml]
2025-05-13 Current progress
    [extras.xml, robot.xml]
2025-05-15 Update robot model and add import script
    [robot.xml]
2025-05-27 Full model working
    [5972k222_ball_bearing__2.stl, ankle__3.stl, ankle__4.stl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]
2025-07-06 Add IsaacLab project
    [5972k222_ball_bearing.stl, 5972k222_ball_bearing__2.stl, 59935k13_ball_joint_rod_end.stl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]
